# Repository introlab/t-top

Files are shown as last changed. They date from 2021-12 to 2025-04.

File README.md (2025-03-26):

# T-Top

T-Top is a tabletop robot designed with advanced audio and vision sensors, deep learning perceptual processing and
telecommunication capabilities to provide richer interaction modalities and develop higher cognitive abilities from
interacting with people.

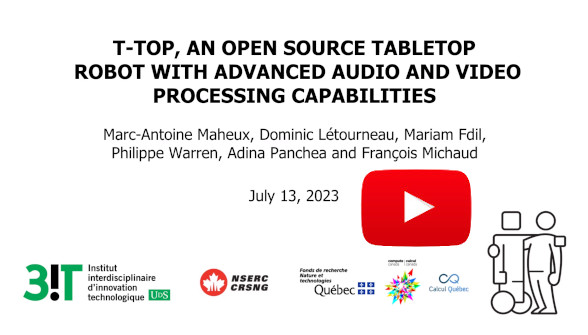
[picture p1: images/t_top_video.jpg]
T-Top (https://www.youtube.com/watch?v=2jpqTp6jozc)


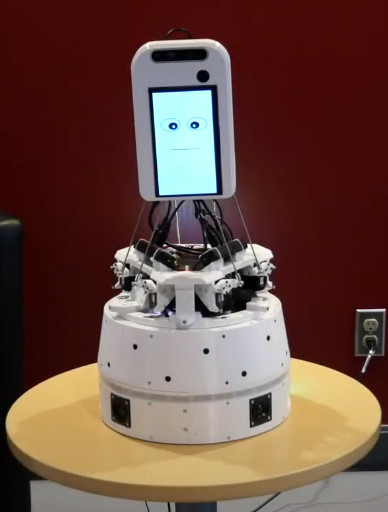
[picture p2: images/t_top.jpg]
T-Top


## Authors

- Marc-Antoine Maheux (@mamaheux)
- Dominic Létourneau (@doumdi)
- Philippe Warren (@philippewarren)
- Mariam Fdil (@MariamFdil)
- [François Michaud](mailto:francois.michaud@usherbrooke.ca), ing., Ph.D.

## Contributors

- Ian-Mathieu Joly (@joli-1801)
- Charles Caya (@chcaya)
- Alexandre Filion (@alexfilion)

## Licensing

- Source code files: [GPLv3](LICENSE_SOURCE_CODE)
- Other files: [Creative Commons Attribution-NonCommercial-ShareAlike 4.0 International Public License](LICENSE_OTHER)

## Features

| Category | Type | Description |
| --- | --- | --- |
| Power | Power Adapter | 19 V |
| | Battery | 1x [RRC2054-2](https://www.rrc-ps.com/en/battery-packs/standard-battery-packs/products/RRC2054-2) |
| | Battery Charger | 1x [RRC-PMM240](https://www.rrc-ps.com/en/battery-packs/standard-battery-packs/products/RRC-PMM240) |
| Sensors | Microphone Array  | 16x [xSoundsMicrophones](https://github.com/introlab/xSoundsMicrophones), 1x [16SoundsUSB](https://github.com/introlab/16SoundsUSB) |
| | RGB-D Camera | 1x [Intel RealSense D435i](https://www.intelrealsense.com/depth-camera-d435i/) |
| | Wide Angle Camera | 1x [Arducam AR0230](https://www.uctronics.com/arducam-1080p-hd-wide-angle-wdr-usb-camera-module-for-computer-2mp-1-2-7-cmos-ar0230-100-degree-mini-uvc-usb2-0-spy-webcam-board-with-3-3ft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) |
| | Touchscreen | 1x 7 inch 1024x600 capacitive touchscreen |
| | Current/Voltage | [INA220](https://www.ti.com/product/INA220) |
| | Light Sensors | 4x [Adafruit ALS-PT19 ](https://www.adafruit.com/product/2748) |
| | Buttons | 4x buttons |
| Actuators | Stewart Platform  | Displacement range: ±3 cm (x, y and z), ±20° (x and y), ±30° (z). Motor: [Dynamixel XL430-W250](https://emanual.robotis.com/docs/en/dxl/x/xl430-w250/) | |
| | Rotating Base | Displacement range: illimited. Motor: [Dynamixel XL430-W250](https://emanual.robotis.com/docs/en/dxl/x/xl430-w250/) |
| | Speakers | 4x [Dayton Audio DMA45-8](https://www.daytonaudio.com/product/1613/dma45-8-1-1-2-dual-magnet-aluminum-cone-full-range-driver-8-ohm), 2x [MAX9744](https://www.adafruit.com/product/1752) |
| | Cooling | 2x [Noctua NF-A4x20 5V](https://noctua.at/en/products/fan/nf-a4x20-5v) |
| | Touchscreen | 1x 7 inch 1024x600 capacitive touchscreen |
| | LED | Battery status, volume level, led strip |
| Network | WiFi | Intel Dual Band Wireless-AC 8265 NGW |
| | Ethernet | 100 Mbps |
| Processing | Computer | [NVIDIA Jetson AGX Xavier Developer Kit](https://developer.nvidia.com/embedded/jetson-agx-xavier-developer-kit) or [NVIDIA Jetson AGX Xavier Orin Developer Kit](https://developer.nvidia.com/embedded/jetson-agx-orin-developer-kit) |
| | Motor MCU | [Teensy 4.0](https://www.pjrc.com/store/teensy40.html) |
| | Battery MCU | [Teensy LC](https://www.pjrc.com/teensy/teensyLC.html) |
| Perceptions | | SLAM, object detection, person pose estimation, face recognition, sound classification, speaker identification, robot name detection, speech to text, person identification, music beat detection, source source localization, ego noise reduction, vad |
| Behaviors | | Telepresence, emotions, talking, greeting, face following, dancing, exploring, sound following |

## Repository Structure

- The [documentation](documentation) folder contains the documentation to build and configure T-Top.
- The [CAD](CAD) folder contains the SolidWorks files of the robot. Il also contains the DXF and STL files to cut and
  print custom parts.
- The [firmwares](firmwares) folder contains the firmware for the MCUs.
- The [PCB](PCB) folder contains the KiCad files of the custom PCBs. Il also contains the Gerber files to manufacture
  the PCBs.
- The [ros](ros) folder contains the ROS packages to use the robot.
- The [tools](tools) folder contains the tools to develop and use the robot.

## Development Computer Setup

See [01_COMPUTER_CONFIGURATION.md](documentation/assembly/01_COMPUTER_CONFIGURATION.md#development-computer-ubuntu-2004)

## Papers

- [M.-A. Maheux, D. Létourneau, P. Warren, A. M. Panchea, J. M. Robillard and F. Michaud, “‍Designing a Tabletop SAR as an Advanced HRI Experimentation Platform,” in Proceedings of the 2024 International Symposium on Technological Advances in Human-Robot Interaction (TAHRI 2024), Boulder, CO, USA, 2024](https://dl.acm.org/doi/10.1145/3648536.3648538)
    - [YouTube Video](https://youtu.be/HSd65F055VE)
- [M. Fdil, M. Levasseur, D. Létourneau, M.-A. Maheux, M. Lussier-Therrien, F. Michaud, "Enhancing Open Conversations Using Visual Percepts From a Socially Assistive Robot -- Preliminary Assessment", in Proceedings of the International Conference on Social Robotics, 2024, pp. 1-12.](https://link.springer.com/chapter/10.1007/978-981-96-3519-1_17)
    - [YouTube Video](https://youtu.be/4ykoxQKUweU)  
- [A. M. Panchea, M.-A. Maheux, P. Warren, D. Létourneau and F. Michaud, “Exploratory Evaluation of a Tabletop Robot With Older Adults,” in Proceedings of the 2024 ACM/IEEE International Conference on Human-Robot Interaction, Boulder, CO, USA, 2024, pp. 817–821.](https://dl.acm.org/doi/10.1145/3610978.3640621)
- [M.-A. Maheux, A. M. Panchea, P. Warren, D. Létourneau and F. Michaud, “T-Top, an Open Source Tabletop Robot with Advanced Onboard Audio, Vision and Deep Learning Capabilities,” in Proceedings of the 2023 IEEE/RSJ International Conference on Intelligent Robots and Systems (IROS), Detroit, MI, USA, 2023, pp. 7862-7869.](https://ieeexplore.ieee.org/abstract/document/10342252)
- [M.-A. Maheux, C. Caya, D. Létourneau and F. Michaud, “T-Top, a sar experimental platform,” in Proceedings of the 2022 ACM/IEEE International Conference on Human-Robot Interaction, 2022, pp. 904–908.](https://dl.acm.org/doi/abs/10.5555/3523760.3523902)

## Sponsor

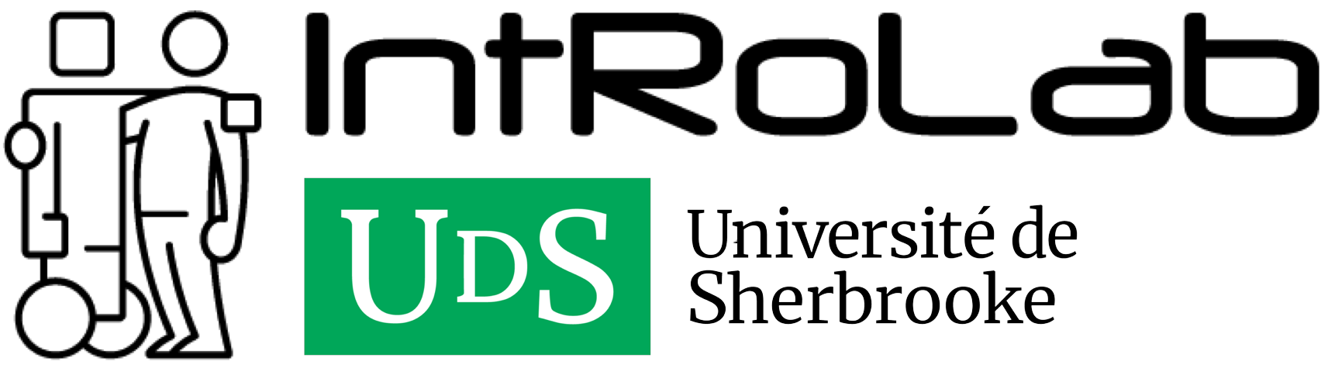
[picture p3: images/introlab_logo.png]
IntRoLab


[IntRoLab - Intelligent / Interactive / Integrated / Interdisciplinary Robot Lab](https://introlab.3it.usherbrooke.ca)

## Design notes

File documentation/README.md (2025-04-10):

# Documentation

## Folder Structure

- The [assembly](assembly/) folder contains the assembly instructions.
- The [protocols](protocols/) folder contains the communication protocols definitions.
- The [architecture](architecture/) folder contains architecture diagrams.
- The [tf](tf/) folder illustrates the frame locations.
- The [hbba_lite](hbba_lite/) folder contains the documentation of how to use HBBA Lite.
- The [getting_started](getting_started/) folder contains the documentation to get started with the robot.

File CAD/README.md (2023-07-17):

# CAD
This folder contains all mechanical-related files. The CAD have been done with SOLIDWORKS. If you don't have SOLIDWORKS, you can open the [STEP file](step/robot.STEP).

## Bill of Materials
 - [Parts](../documentation/assembly/00_ORDER_PRINT_LASER_CUTTING.md#bill-of-materials-excluding-custom-pcbs)
 - [3d Printing](../documentation/assembly/00_ORDER_PRINT_LASER_CUTTING.md#3d-printing)
 - [Laser Cutting](../documentation/assembly/00_ORDER_PRINT_LASER_CUTTING.md#laser-cutting)

## Folder Structure
SolidWorks files:
 - [3d printed parts](3d-printed-parts) contains the SolidWorks files for the 3D printed parts.
 - [assemblies](assemblies) contains the SolidWorks files for the assemblies. The robot assembly file is [robot.SLDASM](assemblies/robot.SLDASM).
 - [electronics](electronics) contains the SolidWorks files for all electronics parts.
 - [gazebo_meshes](gazebo%20meshes) contains the CAD files for the simulation.
 - [hardware](hardware) contains the SolidWorks files for screws, nuts, spacers and rods.
 - [laser](laser) contains the SolidWorks files for the laser cutted parts.
 - [step](step) contains the robot assembly in STEP format.

Manufacture files:
 - [DXF](DXF)
 - [STL](STL)

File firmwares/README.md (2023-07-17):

# Firmwares

T-Top uses two microcontrollers (MCU). This folder contains the firmwares for those.

## Folder Structure

- THe [common](common) folder contains common libraries.
- The [dynamixel_control](dynamixel_control) folder contains the firmware of the MCU that controls the motors.
- The [dynamixel_setup](dynamixel_setup)folder contains the firmware to setup the motors.
- The [psu_control](psu_control) folder contains the firmware of the MCU that controls and monitors the battery, audio
  amplifier, fans and LEDs.
- The [ego_noise_opencr_firmware](ego_noise_opencr_firmware) folder contains the firmware to get the ego noise data.

## Credits

The class `TrustRegionReflectiveSolver` in the [opencr_firmware](opencr_firmware) folder is heavily inspired
by [scipy.optimize.least_squares](https://docs.scipy.org/doc/scipy/reference/generated/scipy.optimize.least_squares.html)
.

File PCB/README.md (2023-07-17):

# PCB
To build T-Top, two cutom PCBs must be made.

## Folder Structure
- The [psu_control](psu_control) folder contains the PCB files for the PCB that controls and monitors the battery, audio amplifier, fans and LEDs.
- The [dynamixel_control](dynamixel_control) folder contains the PCB files for the PCB that controls the Dynamixel motors.
- The [buck_boost](buck_boost) folder contains the PCB files for the Buck-Boost PCB.
- The [t-top.pretty](t-top.pretty) folder contains the custom footprints.
- The [t-top.kicad_sym](t-top.kicad_sym) file contains the custom parts.

## PSU Control PCB
- [Schematic](psu_control/schematic.pdf)
- [Gerber](psu_control/gerber)
- [Bill of Materials](../documentation/assembly/00_ORDER_PRINT_LASER_CUTTING.md#psu-control-pcb)

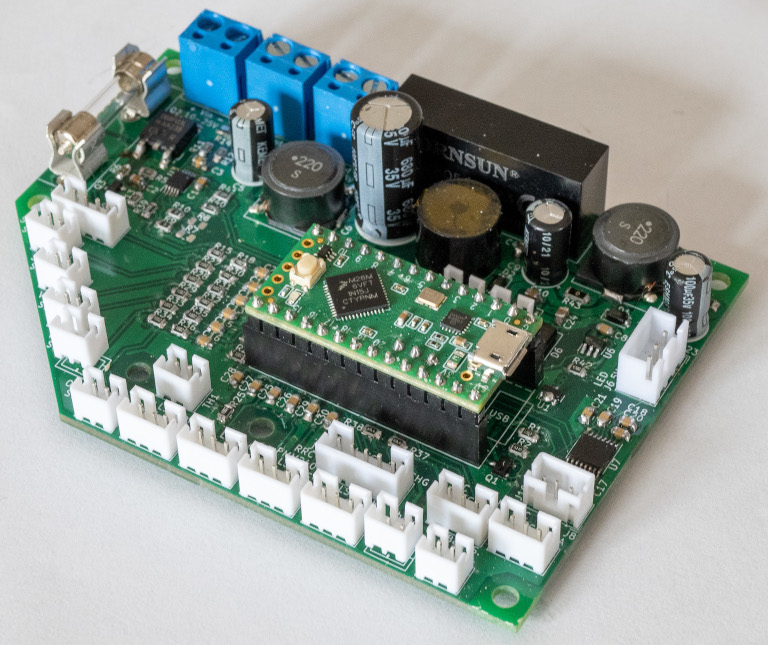
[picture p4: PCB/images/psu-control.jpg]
PSU Control PCB


## Dynamixel Control PCB
- [Schematic](dynamixel_control/schematic.pdf)
- [Gerber](dynamixel_control/gerber)
- [Bill of Materials](../documentation/assembly/00_ORDER_PRINT_LASER_CUTTING.md#dynamixel-control-pcb)

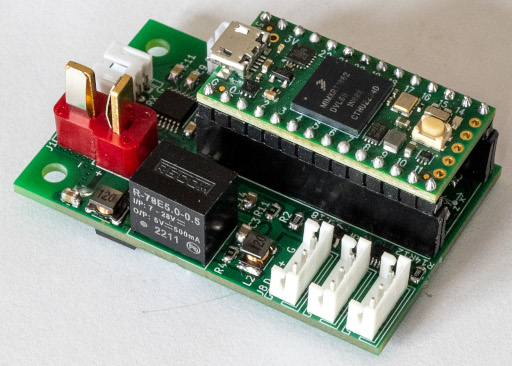
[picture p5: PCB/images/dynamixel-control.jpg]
Dynamixel Control PCB


## Buck-Boost PCB
- [Schematic](buck_boost/schematic.pdf)
- [Gerber](buck_boost/gerber)
- [Bill of Materials](../documentation/assembly/00_ORDER_PRINT_LASER_CUTTING.md#buck-boost-pcb)

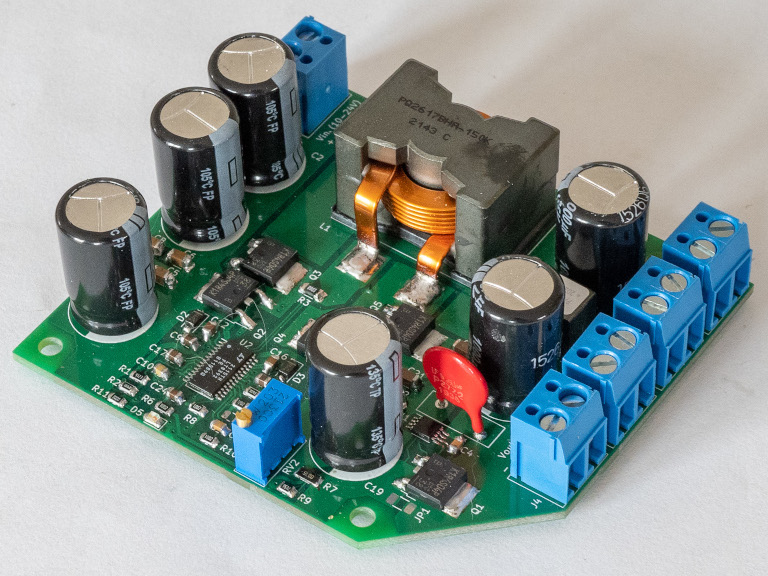
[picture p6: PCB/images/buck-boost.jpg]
Buck-Boost PCB


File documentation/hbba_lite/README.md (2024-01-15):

# HBBA Lite
HBBA (Hybrid Behavior-Based Architecture) is the control architecture of T-Top. A hybrid robot architecture means that perceptual nodes can communicate with the behavior nodes and the planning modules.
T-Top uses [HBBA Lite](https://github.com/introlab/hbba_lite/) implementation instead of the [original one](https://github.com/introlab/HBBA) since HBBA Lite is simpler to use but less complete.

## Core
See the [HBBA Lite documentation](https://github.com/introlab/hbba_lite#documentation).

## T-Top
The following sections present T-Top specific information.

### Resources
- `motor`: The resource to prevent conflicts over the motors.
- `audio`: The resource to prevent conflicts over the sound output.
- `led`: The resource to prevent conflicts over the LEDs.

### Desire Types
- [`Camera3dRecordingDesire`](../../ros/utils/t_top_hbba_lite/include/t_top_hbba_lite/Desires.h#L12): To enable the recording of the 3D camera.
- [`Camera2dWideRecordingDesire`](../../ros/utils/t_top_hbba_lite/include/t_top_hbba_lite/Desires.h#L22): To enable the recording of the 2D Wide camera.
- [`RobotNameDetectorDesire`](../../ros/utils/t_top_hbba_lite/include/t_top_hbba_lite/Desires.h#L32): To enable the robot name detector node.
- [`RobotNameDetectorWithLedStatusDesire`](../../ros/utils/t_top_hbba_lite/include/t_top_hbba_lite/Desires.h#L42): To enable the robot name detector node and have feed on the LED strip.
- [`SlowVideoAnalyzer3dDesire`](../../ros/utils/t_top_hbba_lite/include/t_top_hbba_lite/Desires.h#52): To enable the video analyzer node for the 3D camera at 1 Hz.
- [`FastVideoAnalyzer3dDesire`](../../ros/utils/t_top_hbba_lite/include/t_top_hbba_lite/Desires.h#L62): To enable the video analyzer node for the 3D camera at 5 Hz.
- [`FastVideoAnalyzer3dWithAnalyzedImageDesire`](../../ros/utils/t_top_hbba_lite/include/t_top_hbba_lite/Desires.h#L72): To enable the video analyzer node for the 3D camera at 5 Hz and to publish the analyzed image.
- [`SlowVideoAnalyzer2dWideDesire`](../../ros/utils/t_top_hbba_lite/include/t_top_hbba_lite/Desires.h#L82): To enable the video analyzer node for the 2D wide camera at 1 Hz.
- [`FastVideoAnalyzer2dWideDesire`](../../ros/utils/t_top_hbba_lite/include/t_top_hbba_lite/Desires.h#92): To enable the video analyzer node for the 2D wide camera at 5 Hz.
- [`FastVideoAnalyzer2dWideWithAnalyzedImageDesire`](../../ros/utils/t_top_hbba_lite/include/t_top_hbba_lite/Desires.h#L102): To enable the video analyzer node for the 2D wide camera at 5 Hz and to publish the analyzed image.
- [`AudioAnalyzerDesire`](../../ros/utils/t_top_hbba_lite/include/t_top_hbba_lite/Desires.h#L112): To enable the audio analyzer node.
- [`VadDesire`](../../ros/utils/t_top_hbba_lite/include/t_top_hbba_lite/Desires.h#L122): To enable to VAD node.
- [`SpeechToTextDesire`](../../ros/utils/t_top_hbba_lite/include/t_top_hbba_lite/Desires.h#L132): To enable the speech to text node.
- [`ExploreDesire`](../../ros/utils/t_top_hbba_lite/include/t_top_hbba_lite/Desires.h#L142): To enable the explore node.
- [`FaceAnimationDesire`](../../ros/utils/t_top_hbba_lite/include/t_top_hbba_lite/Desires.h#L152): To change the face animation.
- [`LedEmotionDesire`](../../ros/utils/t_top_hbba_lite/include/t_top_hbba_lite/Desires.h#L175): To enable the led emotion node.
- [`LedAnimationDesire`](../../ros/utils/t_top_hbba_lite/include/t_top_hbba_lite/Desires.h#L197): To enable the led animation node.
- [`SoundFollowingDesire`](../../ros/utils/t_top_hbba_lite/include/t_top_hbba_lite/Desires.h#L245): To enable the node that makes T-Top follow the loudest sound.
- [`NearestFaceFollowingDesire`](../../ros/utils/t_top_hbba_lite/include/t_top_hbba_lite/Desires.h#L255): To enable the node that makes T-Top follow the nearest face.
- [`SpecificFaceFollowingDesire`](../../ros/utils/t_top_hbba_lite/include/t_top_hbba_lite/Desires.h#L265): To enable the node that makes T-Top follow a specific face.
- [`SoundObjectPersonFollowingDesire`](../../ros/utils/t_top_hbba_lite/include/t_top_hbba_lite/Desires.h#L284): To enable the node that makes T-Top follow the loudest sound, the people and the objects.
- [`TalkDesire`](../../ros/utils/t_top_hbba_lite/include/t_top_hbba_lite/Desires.h#L294): To make T-Top talk.
- [`GestureDesire`](../../ros/utils/t_top_hbba_lite/include/t_top_hbba_lite/Desires.h#L313): To make T-Top perform a head gesture.
- [`DanceDesire`](../../ros/utils/t_top_hbba_lite/include/t_top_hbba_lite/Desires.h#L335): To make T-Top dance.
- [`PlaySoundDesire`](../../ros/utils/t_top_hbba_lite/include/t_top_hbba_lite/Desires.h#L345): To make T-Top play a sound file.
- [`TelepresenceDesire`](../../ros/utils/t_top_hbba_lite/include/t_top_hbba_lite/Desires.h#L364): To make T-Top perform a video call
- [`TeleoperationDesire`](../../ros/utils/t_top_hbba_lite/include/t_top_hbba_lite/Desires.h#L374): To enable remote control of T-Top.
- [`TooCloseReactionDesire`](../../ros/utils/t_top_hbba_lite/include/t_top_hbba_lite/Desires.h#L384): To enable the too near reaction behavior.

### Strategies
The strategies are declared in the following files: [Strategies.h](../../ros/utils/t_top_hbba_lite/include/t_top_hbba_lite/Strategies.h) and [Strategies.cpp](../../ros/utils/t_top_hbba_lite/src/Strategies.cpp).

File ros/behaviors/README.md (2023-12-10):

# Behavior Nodes

This folder contains ROS packages for the behavior nodes.

## Folder Structure

- The [dance](dance) folder contains the node to make T-Top dance.
- The [explore](explore) folder contains the node to make T-Top explore its surrounding.
- The [face_following](face_following) folder contains the node to make T-Top follow the nearest face.
- The [gesture](gesture) folder contains the node to make T-Top perform gestures.
- The [led_emotions](led_emotions) folder contains the node to make T-Top express emotion with its LED strip.
- The [led_animations](led_animations) folder contains the node to perform animations with the LED strip.
- The [sound_following](sound_following) folder contains the node to make T-Top follow the loudest sound.
- The [sound_object_person_following](sound_object_person_following) folder contains the node to make T-Top follow the loudest sound, the biggest (nearest) person and some objects.
- The [sound_player](sound_player) folder contains the node to play sound files.
- The [talk](talk) folder contains the node to make T-Top talk.
- The [piper_ros](piper_ros) folder contains the node to generate speech files with [Piper](https://github.com/rhasspy/piper).
- The [too_close_reaction](too_close_reaction) folder contains the node to move back the head when someone is too close to T-Top.

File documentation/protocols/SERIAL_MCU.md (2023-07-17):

# Serial MCU Communucation Protocol
This document presents the serial communication protocol between the MCUs and the computer.

## General Format
It is a binary protocol and all fields use little-endian ordering.

<table>
    <thead>
        <tr>
            <th colspan="9">Bytes</th>
        </tr>
    </thead>
    <thead>
        <tr>
            <th>1</th>
            <th>2</th>
            <th>3</th>
            <th>4</th>
            <th>5</th>
            <th>6</th>
            <th>7</th>
            <th>8</th>
        </tr>
    </thead>
    <tbody>
        <tr>
            <td colspan="4">Preamble</td>
            <td>Full Message Length</td>
            <td>Message Source Id</td>
            <td>Message Destination Id</td>
            <td>Acknowledgment Needed</td>
        </tr>
        <tr>
            <td colspan="2">Message Id</td>
            <td colspan="2">Message Type</td>
            <td colspan="4">Payload</td>
        </tr>
        <tr>
            <td colspan="8">...</td>
        </tr>
        <tr>
            <td>CRC8</td>
            <td colspan="7"></td>
        </tr>
    </tbody>
</table>

### Field Description
| Field Name | Type | Description |
| --- | --- | --- |
| Preamble | uint32 | This field is used to detect the beginning of a message (0xAAAAAAAA). |
| Full Message Length | uint8  | This field is equal to the message length in bytes including this field and without the preamble. |
| Message Source Id | uint8  | This field contains the device id of the source device. |
| Message Destination Id | uint8  | This field contains the device id of the destination device. |
| Acknowledgment Needed  | bool | This field indicates if an acknowledgment is needed). |
| Message Id | uint16 | This field contains a random id identifying the message. |
| Message Type | uint16 | This field contains the message type. |
| Payload | | The payload depends on the message type. |
| CRC8 | uint8  | This field contains the CRC8 value excluding this field. |

### Device Id Descriptions
| Device Id | Name |
| --- | --- |
| 0 | PSU Control |
| 1 | Dynamixel Control |
| 2 | Computer |

### Message Types
| Message Type | Name | Source | Destination | Description |
| --- | --- | --- | --- | --- |
| 0 | [Acknowledgment](#acknowledgment-payload) | Any | Any | This message indicates that a message is received. |
| 1 | [Base Status](#base-Status-payload) | PSU Control | Computer | This message contains the status of the base. |
| 2 | [Button Pressed](#button-pressed-payload) | PSU Control | Computer | This message indicates that a button is pressed. |
| 3 | [Set Volume](#set-volume-payload) | Computer | PSU Control | This message sets the volume of the audio amplifier. |
| 4 | [Set LED Colors](#set-led-colors-payload) | Computer | PSU Control | This message sets the LED colors of the base. |
| 5 | [Motor Status](#motor-status-payload) | Dynamixel Control | Computer | This message contains the status of all motors. |
| 6 | [IMU Data](#imu-data-payload) | Dynamixel Control | Computer | This message contains the IMU data. |
| 7 | [Set Torso Orientation](#set-torso-orientation-payload) | Computer | Dynamixel Control | This message sets the torso orientation. |
| 8 | [Set Head Pose](#set-head-pose-payload) | Computer | Dynamixel Control | This message sets the head pose. |
| 9 | Shutdown | PSU Control | Computer/Dynamixel Control | This message indicates that the computer must shut down. This message has no payload. |

### Behaviors
- All receivers check the preamble to detect the beginning of a message. So, a byte can be missed and the receivers are not out of synchronization with the senders. Only the message containing the missing byte is dropped.
- All devices route the message according to the destination id.
- The message is dropped if the destination id is invalid.
- The message is dropped if the source id is invalid.
- The message is dropped if the CRC8 is invalid.
- The message is dropped if the length does not match the message type.
- The destination device sends an acknowledgment to the source device if the CRC8 is valid.

## Acknowledgment Payload
This message indicates that a message is received.

<table>
    <thead>
        <tr>
            <th colspan="2">Bytes</th>
        </tr>
    </thead>
    <thead>
        <tr>
            <th>1</th>
            <th>2</th>
        </tr>
    </thead>
    <tbody>
        <tr>
            <td colspan="2">Received Message Id</td>
        </tr>
    </tbody>
</table>

### Field Description
| Field Name | Type | Description |
| --- | --- | --- |
| Received Message Id | uint16 | This field contains the received message id. |

## Base Status Payload
This message contains the status of the base.

<table>
    <thead>
        <tr>
            <th colspan="8">Bytes</th>
        </tr>
    </thead>
    <thead>
        <tr>
            <th>1</th>
            <th>2</th>
            <th>3</th>
            <th>4</th>
            <th>5</th>
            <th>6</th>
            <th>7</th>
            <th>8</th>
        </tr>
    </thead>
    <tbody>
        <tr>
            <td>Is PSU Connected</td>
            <td>Has Charger Error</td>
            <td>Is Battery Charging</td>
            <td>Has Battery Error</td>
            <td colspan="4">State of Charge</td>
        </tr>
        <tr>
            <td colspan="4">Current</td>
            <td colspan="4">Voltage</td>
        </tr>
        <tr>
            <td colspan="4">Onboard Temperature</td>
            <td colspan="4">External Temperature</td>
        </tr>
        <tr>
            <td colspan="4">Front Light Sensor</td>
            <td colspan="4">Back Light Sensor</td>
        </tr>
        <tr>
            <td colspan="4">Left Light Sensor</td>
            <td colspan="4">Right Light Sensor</td>
        </tr>
        <tr>
            <td>Volume</td>
            <td>Maximum Volume</td>
            <td colspan="6"></td>
        </tr>
    </tbody>
</table>

### Field Description
| Field Name | Type | Description |
| --- | --- | --- |
| Is PSU Connected | bool | This field indicates whether the PSU is connected to the robot. |
| Has Charger Error | bool | This field indicates whether there is a charger error. |
| Is Battery Charging | bool | This field indicates whether the battery is charging. |
| Has Battery Error | bool | This field indicates whether there is a battery error. |
| State of Charge | float  | This field contains the actual battery state of charge in percent (0 to 100). |
| Current | float  | This field contains the actual current in A. |
| Voltage | float  | This field contains the actual voltage in V. |
| Onboard Temperature | float  | This field contains the actual temperature in °C on the PSU Control PCB. |
| External Temperature | float  | This field contains the actual temperature in °C in the base (invalid). |
| Front Light Sensor | float  | This field contains the front light level (0 to 1). |
| Back Light Sensor | float  | This field contains the back light level (0 to 1). |
| Left Light Sensor | float  | This field contains the left light level (0 to 1). |
| Right Light Sensor | float  | This field contains the right light level (0 to 1). |
| Volume | uint8  | This field contains the actual volume (0 to 63). |
| Maximum Volume | uint8  | This field contains the actual volume maximum (0 to 63). The maximum depends on whether the power supply is connected. |

## Button Pressed Payload
This message indicates that a button is pressed.

<table>
    <thead>
        <tr>
            <th>Bytes</th>
        </tr>
    </thead>
    <thead>
        <tr>
            <th>1</th>
        </tr>
    </thead>
    <tbody>
        <tr>
            <td>Button Id</td>
        </tr>
    </tbody>
</table>

### Field Description
| Field Name | Type  | Description |
| --- | ----- | --- |
| Button Id  | uint8 | This field indicates which button was pressed (start or stop). |

### Device Id Descriptions
| Button Id | Name  |
| --- | ----- |
| 0 | Start |
| 1 | End |

## Set Volume Payload
This message sets the volume of the audio amplifier.

<table>
    <thead>
        <tr>
            <th>Bytes</th>
        </tr>
    </thead>
    <thead>
        <tr>
            <th>1</th>
        </tr>
    </thead>
    <tbody>
        <tr>
            <td>Volume</td>
        </tr>
    </tbody>
</table>

### Field Description
| Field Name | Type  | Description |
| --- | ----- | --- |
| Volume | uint8 | This field contains the new volume (0 to 63). |

## Set LED Colors Payload
This message sets the volume of the audio amplifier.

<table>
    <thead>
        <tr>
            <th colspan="8">Bytes</th>
        </tr>
    </thead>
    <thead>
        <tr>
            <th>1</th>
            <th>2</th>
            <th>3</th>
            <th>4</th>
            <th>5</th>
            <th>6</th>
            <th>7</th>
            <th>8</th>
        </tr>
    </thead>
    <tbody>
        <tr>
            <td>LED 1 Red Value</td>
            <td>LED 1 Green Value</td>
            <td>LED 1 Blue Value</td>
            <td>LED 2 Red Value</td>
            <td>LED 2 Green Value</td>
            <td>LED 2 Blue Value</td>
            <td colspan="2">...</td>
        </tr>
    </tbody>
</table>

### Field Description
| Field Name | Type  | Description |
| --- | ----- | --- |
| LED 1 Red Value | uint8 | This field contains the LED 1 red value (0 to 255). |
| LED 1 Green Value | uint8 | This field contains the LED 1 red value (0 to 255). |
| LED 1 Blue Value  | uint8 | This field contains the LED 1 red value (0 to 255). |
| LED 2 Red Value | uint8 | This field contains the LED 2 red value (0 to 255). |
| LED 2 Green Value | uint8 | This field contains the LED 2 red value (0 to 255). |
| LED 2 Blue Value  | uint8 | This field contains the LED 2 red value (0 to 255). |
| ... | | Those fields are repeated for each led. There are 31 LEDs |

## Motor Status Payload
This message contains the status of all motors.

<table>
    <thead>
        <tr>
            <th colspan="8">Bytes</th>
        </tr>
    </thead>
    <thead>
        <tr>
            <th>1</th>
            <th>2</th>
            <th>3</th>
            <th>4</th>
            <th>5</th>
            <th>6</th>
            <th>7</th>
            <th>8</th>
        </tr>
    </thead>
    <tbody>
        <tr>
            <td colspan="4">Torso Orientation</td>
            <td colspan="2">Torso Servo Speed</td>
            <td colspan="2">Head Servo Angle 1</td>
        </tr>
        <tr>
            <td colspan="2">Head Servo Angle 1</td>
            <td colspan="4">Head Servo Angle 2</td>
            <td colspan="2">Head Servo Angle 3</td>
        </tr>
        <tr>
            <td colspan="2">Head Servo Angle 3</td>
            <td colspan="4">Head Servo Angle 4</td>
            <td colspan="2">Head Servo Angle 5</td>
        </tr>
        <tr>
            <td colspan="2">Head Servo Angle 5</td>
            <td colspan="4">Head Servo Angle 6</td>
            <td colspan="2">Head Servo Speed 1</td>
        </tr>
        <tr>
            <td colspan="2">Head Servo Speed 2</td>
            <td colspan="2">Head Servo Speed 3</td>
            <td colspan="2">Head Servo Speed 4</td>
            <td colspan="2">Head Servo Speed 5</td>
        </tr>
        <tr>
            <td colspan="2">Head Servo Speed 6</td>
            <td colspan="4">Head Pose Position X</td>
            <td colspan="2">Head Pose Position Y</td>
        </tr>
        <tr>
            <td colspan="2">Head Pose Position Y</td>
            <td colspan="4">Head Pose Position Z</td>
            <td colspan="2">Head Pose Orientation W</td>
        </tr>
        <tr>
            <td colspan="2">Head Pose Orientation W</td>
            <td colspan="4">Head Pose Orientation X</td>
            <td colspan="2">Head Pose Orientation Y</td>
        </tr>
        <tr>
            <td colspan="2">Head Pose Orientation Y</td>
            <td colspan="4">Head Pose Orientation Z</td>
            <td>Is Head Pose Reachable</td>
            <td></td>
        </tr>
    </tbody>
</table>

### Field Description
| Field Name | Type  | Description |
| --- | ----- | --- |
| Torso Orientation | float | This field contains the actual torso orientation in radian (0 to 2PI). |
| Torso Servo Speed | int16 | This field contains the actual torso servo speed in 0.229 rpm (-1023 to 1023). |
| Head Servo Angle 1 | float | This field contains the actual head servo angle 1 in radian (0 to 2PI). |
| Head Servo Angle 2 | float | This field contains the actual head servo angle 2 in radian (0 to 2PI). |
| Head Servo Angle 3 | float | This field contains the actual head servo angle 3 in radian (0 to 2PI). |
| Head Servo Angle 4 | float | This field contains the actual head servo angle 4 in radian (0 to 2PI). |
| Head Servo Angle 5 | float | This field contains the actual head servo angle 5 in radian (0 to 2PI). |
| Head Servo Angle 6 | float | This field contains the actual head servo angle 6 in radian (0 to 2PI). |
| Head Servo Speed 1 | int16 | This field contains the actual head servo speed 1 in 0.229 rpm (-1023 to 1023). |
| Head Servo Speed 2 | int16 | This field contains the actual head servo speed 2 in 0.229 rpm (-1023 to 1023). |
| Head Servo Speed 3 | int16 | This field contains the actual head servo speed 3 in 0.229 rpm (-1023 to 1023). |
| Head Servo Speed 4 | int16 | This field contains the actual head servo speed 4 in 0.229 rpm (-1023 to 1023). |
| Head Servo Speed 5 | int16 | This field contains the actual head servo speed 5 in 0.229 rpm (-1023 to 1023). |
| Head Servo Speed 6 | int16 | This field contains the actual head servo speed 6 in 0.229 rpm (-1023 to 1023). |
| Head Pose Position X | float | This field contains the actual X head position in meters in frame `stewart_base`. |
| Head Pose Position Y | float | This field contains the actual Y head position in meters in frame `stewart_base`. |
| Head Pose Position Z | float | This field contains the actual Z head position in meters in frame `stewart_base`. |
| Head Pose Orientation W | float | This field contains the actual W head orientation in meters in frame `stewart_base`. |
| Head Pose Orientation X | float | This field contains the actual X head orientation in meters in frame `stewart_base`. |
| Head Pose Orientation Y | float | This field contains the actual Y head orientation in meters in frame `stewart_base`. |
| Head Pose Orientation Z | float | This field contains the actual Z head orientation in meters in frame `stewart_base`. |
| Is Head Pose Reachable  | bool  | This field indicates if the last desired head pose is reachable. |

## IMU Data Payload
This message contains the status of all motors.

<table>
    <thead>
        <tr>
            <th colspan="8">Bytes</th>
        </tr>
    </thead>
    <thead>
        <tr>
            <th>1</th>
            <th>2</th>
            <th>3</th>
            <th>4</th>
            <th>5</th>
            <th>6</th>
            <th>7</th>
            <th>8</th>
        </tr>
    </thead>
    <tbody>
        <tr>
            <td colspan="4">Acceleration X</td>
            <td colspan="4">Acceleration Y</td>
        </tr>
        <tr>
            <td colspan="4">Acceleration Z</td>
            <td colspan="4">Angular Rate X</td>
        </tr>
        <tr>
            <td colspan="4">Angular Rate Y</td>
            <td colspan="4">Angular Rate Z</td>
        </tr>
    </tbody>
</table>

### Field Description
| Field Name | Type  | Description |
| --- | ----- | --- |
| Acceleration X | float | This field contains the actual IMU X Acceleration in m/s².  |
| Acceleration Y | float | This field contains the actual IMU Y Acceleration in m/s².  |
| Acceleration Z | float | This field contains the actual IMU Z Acceleration in m/s².  |
| Angular Rate X | float | This field contains the actual IMU X Angular Rate in rad/s. |
| Angular Rate Y | float | This field contains the actual IMU X Angular Rate in rad/s. |
| Angular Rate Z | float | This field contains the actual IMU X Angular Rate in rad/s. |

## Set Torso Orientation Payload
This message sets the torso orientation.

<table>
    <thead>
        <tr>
            <th colspan="8">Bytes</th>
        </tr>
    </thead>
    <thead>
        <tr>
            <th>1</th>
            <th>2</th>
            <th>3</th>
            <th>4</th>
        </tr>
    </thead>
    <tbody>
        <tr>
            <td colspan="4">Torso Orientation</td>
        </tr>
    </tbody>
</table>

### Field Description
| Field Name | Type  | Description |
| --- | ----- | --- |
| Torso Orientation | float | This field contains the new torso orientation in radian (0 to 2PI). |

## Set Head Pose Payload
This message sets the head pose.

<table>
    <thead>
        <tr>
            <th colspan="8">Bytes</th>
        </tr>
    </thead>
    <thead>
        <tr>
            <th>1</th>
            <th>2</th>
            <th>3</th>
            <th>4</th>
            <th>5</th>
            <th>6</th>
            <th>7</th>
            <th>8</th>
        </tr>
    </thead>
    <tbody>
        <tr>
            <td colspan="4">Head Pose Position X</td>
            <td colspan="4">Head Pose Position Y</td>
        </tr>
        <tr>
            <td colspan="4">Head Pose Position Z</td>
            <td colspan="4">Head Pose Orientation W</td>
        </tr>
        <tr>
            <td colspan="4">Head Pose Orientation X</td>
            <td colspan="4">Head Pose Orientation Y</td>
        </tr>
        <tr>
            <td colspan="4">Head Pose Orientation Z</td>
            <td colspan="4"></td>
        </tr>
    </tbody>
</table>

### Field Description
| Field Name | Type  | Description |
| --- | ----- | --- |
| Head Pose Position X | float | This field contains the new X head position in meters in frame `stewart_base`. |
| Head Pose Position Y | float | This field contains the new Y head position in meters in frame `stewart_base`. |
| Head Pose Position Z | float | This field contains the new Z head position in meters in frame `stewart_base`. |
| Head Pose Orientation W | float | This field contains the new W head orientation in meters in frame `stewart_base`. |
| Head Pose Orientation X | float | This field contains the new X head orientation in meters in frame `stewart_base`. |
| Head Pose Orientation Y | float | This field contains the new Y head orientation in meters in frame `stewart_base`. |
| Head Pose Orientation Z | float | This field contains the new Z head orientation in meters in frame `stewart_base`. |

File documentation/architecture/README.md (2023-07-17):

# Architecture
This folder contains architecture diagrams. All diagrams have been done with [diagrams.net](diagrams.net).

## Electrical Block Diagram
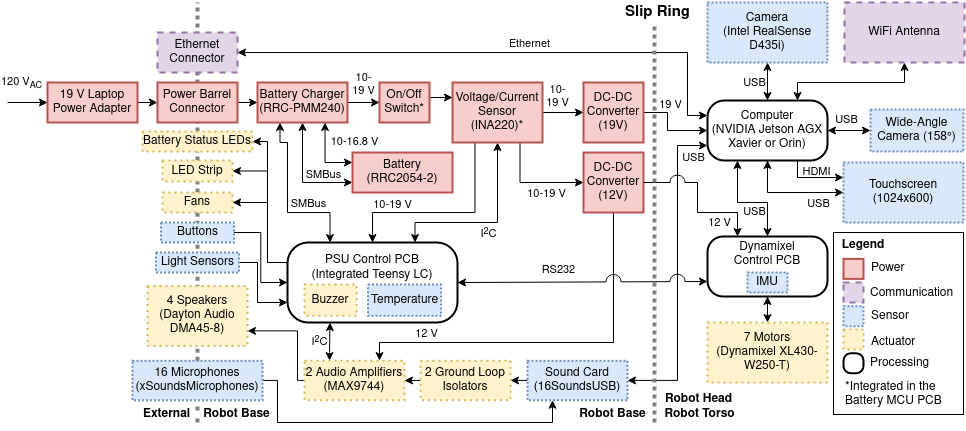
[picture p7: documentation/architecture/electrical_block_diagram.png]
Electrical Block Diagram


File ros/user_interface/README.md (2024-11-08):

# user_interface

This folder contains the web user interface for the robot face.

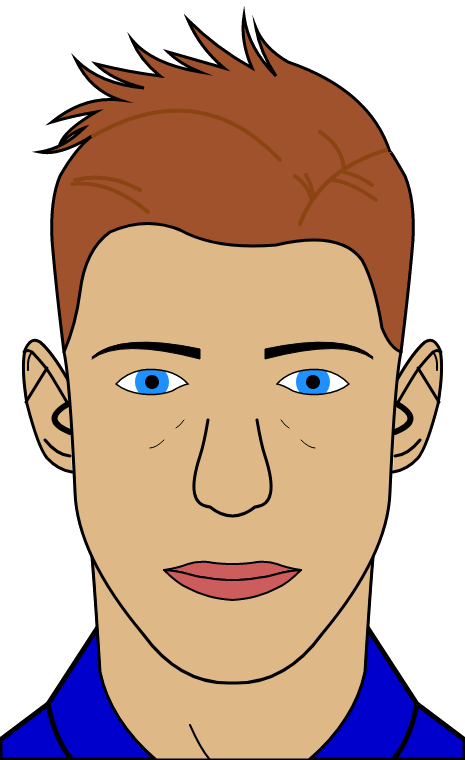
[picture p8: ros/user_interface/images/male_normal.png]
Male

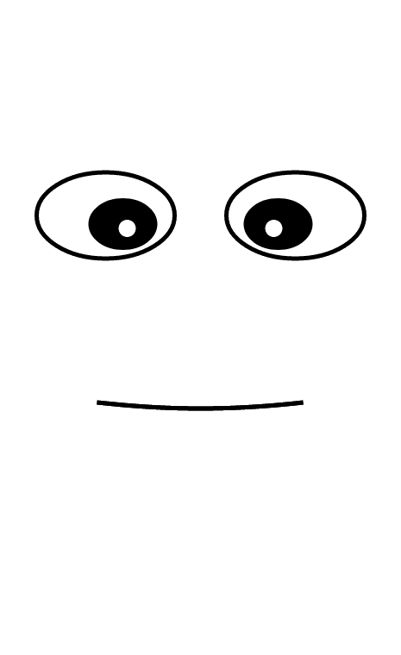
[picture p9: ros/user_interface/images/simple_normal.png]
Simple


## Package setup

```
npm install
```

## Compiles and hot-reloads for development

```
npm run serve
```

## Published Topics

- `face/animation` ([std_msgs/String](https://docs.ros.org/en/humble/p/std_msgs/interfaces/msg/String.html)): Indicates the
  actual animation.
- `face/mouth_signal_scale` ([std_msgs/Float32](https://docs.ros.org/en/humble/p/std_msgs/interfaces/msg/Float32.html)):
  Indicates how much the mouth must be open.

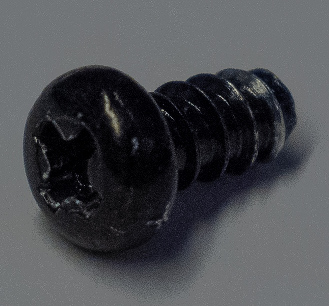
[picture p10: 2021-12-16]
documentation/assembly/images/hardware/dynamixel-screw.jpg

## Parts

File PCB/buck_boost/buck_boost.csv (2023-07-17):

Source: | /home/marc-antoine/Bureau/Maitrîse/t-top_ws/src/t-top/PCB/buck_boost/buck_boost.kicad_sch
Date: | lun 17 avr 2023 14:18:07
Tool: | Eeschema 6.0.11-2627ca5db0~126~ubuntu20.04.1
Generator: | /usr/share/kicad/plugins/bom_csv_grouped_by_value.py
Component Count: | 57
Individual Components:
Item | Qty | Reference(s) | Value | LibPart | Footprint | Datasheet
 |  | C1 | 1000µF/35V | Device:CP | Capacitor_THT:CP_Radial_D12.5mm_P5.00mm
 |  | C2 | 1000µF/35V | Device:CP | Capacitor_THT:CP_Radial_D12.5mm_P5.00mm
 |  | C3 | 1000µF/35V | Device:CP | Capacitor_THT:CP_Radial_D12.5mm_P5.00mm
 |  | C4 | 47nF/35V | Device:C | Capacitor_SMD:C_0805_2012Metric | ~
 |  | C5 | 10µF/35V | Device:C | Capacitor_SMD:C_1206_3216Metric | ~
 |  | C6 | 10µF/35V | Device:C | Capacitor_SMD:C_1206_3216Metric | ~
 |  | C7 | 10µF/35V | Device:C | Capacitor_SMD:C_1206_3216Metric | ~
 |  | C8 | 10µF/35V | Device:C | Capacitor_SMD:C_1206_3216Metric | ~
 |  | C9 | 1µF/35V | Device:C | Capacitor_SMD:C_0805_2012Metric | ~
 |  | C10 | 0.47µF/16V | Device:C | Capacitor_SMD:C_0805_2012Metric | ~
 |  | C11 | 1000µF/35V | Device:CP | Capacitor_THT:CP_Radial_D12.5mm_P5.00mm
 |  | C12 | 2.2µF/16V | Device:C | Capacitor_SMD:C_0805_2012Metric | ~
 |  | C13 | 220nF/16V | Device:C | Capacitor_SMD:C_0805_2012Metric | ~
 |  | C14 | 27nF/16V | Device:C | Capacitor_SMD:C_0805_2012Metric | ~
 |  | C15 | NI | Device:C | Capacitor_SMD:C_0805_2012Metric | ~
 |  | C16 | 2.2µF/16V | Device:C | Capacitor_SMD:C_0805_2012Metric | ~
 |  | C17 | 4.7µF/16V | Device:C | Capacitor_SMD:C_0805_2012Metric | ~
 |  | C18 | 1µF/35V | Device:C | Capacitor_SMD:C_0805_2012Metric | ~
 |  | C19 | 470µF/35V | Device:CP | Capacitor_THT:CP_Radial_D12.5mm_P5.00mm
 |  | C20 | 22µF/35V | Device:C | Capacitor_SMD:C_1206_3216Metric | ~
 |  | C21 | 22µF/35V | Device:C | Capacitor_SMD:C_1206_3216Metric | ~
 |  | C22 | 22µF/35V | Device:C | Capacitor_SMD:C_1206_3216Metric | ~
 |  | C23 | 22µF/35V | Device:C | Capacitor_SMD:C_1206_3216Metric | ~
 |  | C24 | 1µF/35V | Device:C | Capacitor_SMD:C_0805_2012Metric | ~
 |  | C25 | 1000µF/35V | Device:CP | Capacitor_THT:CP_Radial_D12.5mm_P5.00mm
 |  | D2 | SS2040LL | Device:D_Schottky | Diode_SMD:D_SOD-123F | ~
 |  | D3 | SS2040LL | Device:D_Schottky | Diode_SMD:D_SOD-123F | ~
 |  | D5 | LED | Device:LED | Diode_SMD:D_0805_2012Metric | ~
 |  | J1 | VIN 10-24V | Connector:Conn_01x02_Male | t-top:OSTTA020161 | ~
 |  | J2 | VOUT | Connector:Conn_01x02_Male | t-top:OSTTA020161 | ~
 |  | J3 | VOUT | Connector:Conn_01x02_Male | t-top:OSTTA020161 | ~
 |  | J4 | VOUT | Connector:Conn_01x02_Male | t-top:OSTTA020161 | ~
 |  | J5 | VOUT | Connector:Conn_01x02_Male | t-top:OSTTA020161 | ~
 |  | JP1 | Jumper | Device:Jumper | Resistor_SMD:R_1206_3216Metric
 |  | L1 | 15µH (PQ2617BHA-150K) | Device:L | t-top:PQ2617BHA-150K | ~
 |  | L2 | 1µH (PA4987.102HLT) | Device:L | t-top:PA4987.XXXHL | ~
 |  | Q1 | TK1R4S04PB | Device:Q_NMOS_GDS | Package_TO_SOT_SMD:TO-252-2 | ~
 |  | Q2 | TK1R4S04PB | Device:Q_NMOS_GDS | Package_TO_SOT_SMD:TO-252-2 | ~
 |  | Q3 | TK1R4S04PB | Device:Q_NMOS_GDS | Package_TO_SOT_SMD:TO-252-2 | ~
 |  | Q4 | TK1R4S04PB | Device:Q_NMOS_GDS | Package_TO_SOT_SMD:TO-252-2 | ~
 |  | Q5 | TK1R4S04PB | Device:Q_NMOS_GDS | Package_TO_SOT_SMD:TO-252-2 | ~
 |  | R1 | 412k | Device:R | Resistor_SMD:R_0805_2012Metric | ~
 |  | R2 | 80.6k | Device:R | Resistor_SMD:R_0805_2012Metric | ~
 |  | R3 | 0.003/1W | Device:R | Resistor_SMD:R_1206_3216Metric | ~
 |  | R4 | 12k | Device:R | Resistor_SMD:R_0805_2012Metric | ~
 |  | R5 | 309k | Device:R | Resistor_SMD:R_0805_2012Metric | ~
 |  | R6 | 10k | Device:R | Resistor_SMD:R_0805_2012Metric | ~
 |  | R7 | RIS | Device:R | Resistor_SMD:R_1206_3216Metric | ~
 |  | R8 | 10k | Device:R | Resistor_SMD:R_0805_2012Metric | ~
 |  | R9 | FB3 | Device:R | Resistor_SMD:R_0805_2012Metric | ~
 |  | R10 | 10k | Device:R | Resistor_SMD:R_0805_2012Metric | ~
 |  | R11 | 301 | Device:R | Resistor_SMD:R_0805_2012Metric | ~
 |  | R12 | 0 | Device:R | Resistor_SMD:R_1206_3216Metric | ~
 |  | RV1 | V27ZA2P | Device:Varistor | Varistor:RV_Disc_D12mm_W4.2mm_P7.5mm | ~
 |  | RV2 | 20k | Device:R_POT | Potentiometer_THT:Potentiometer_Bourns_3296W_Vertical
 |  | U1 | LTC4359-MS8 | Power_Management:LTC4359-MS8 | Package_SO:MSOP-8_3x3mm_P0.65mm | https://www.analog.com/media/en/technical-documentation/data-sheets/ltc4359.pdf
 |  | U2 | LT8392 | t-top:LT8392 | Package_SO:TSSOP-28-1EP_4.4x9.7mm_P0.65mm
Collated Components:
Item | Qty | Reference(s) | Value | LibPart | Footprint | Datasheet
1 | 5 | C1, C2, C3, C11, C25 | 1000µF/35V | Device:CP | Capacitor_THT:CP_Radial_D12.5mm_P5.00mm
2 | 1 | C4 | 47nF/35V | Device:C | Capacitor_SMD:C_0805_2012Metric | ~
3 | 4 | C5, C6, C7, C8 | 10µF/35V | Device:C | Capacitor_SMD:C_1206_3216Metric | ~
4 | 3 | C9, C18, C24 | 1µF/35V | Device:C | Capacitor_SMD:C_0805_2012Metric | ~
5 | 1 | C10 | 0.47µF/16V | Device:C | Capacitor_SMD:C_0805_2012Metric | ~
6 | 2 | C12, C16 | 2.2µF/16V | Device:C | Capacitor_SMD:C_0805_2012Metric | ~
7 | 1 | C13 | 220nF/16V | Device:C | Capacitor_SMD:C_0805_2012Metric | ~
8 | 1 | C14 | 27nF/16V | Device:C | Capacitor_SMD:C_0805_2012Metric | ~
9 | 1 | C15 | NI | Device:C | Capacitor_SMD:C_0805_2012Metric | ~
10 | 1 | C17 | 4.7µF/16V | Device:C | Capacitor_SMD:C_0805_2012Metric | ~
11 | 1 | C19 | 470µF/35V | Device:CP | Capacitor_THT:CP_Radial_D12.5mm_P5.00mm
12 | 4 | C20, C21, C22, C23 | 22µF/35V | Device:C | Capacitor_SMD:C_1206_3216Metric | ~
13 | 2 | D2, D3 | SS2040LL | Device:D_Schottky | Diode_SMD:D_SOD-123F | ~
14 | 1 | D5 | LED | Device:LED | Diode_SMD:D_0805_2012Metric | ~
15 | 1 | J1 | VIN 10-24V | Connector:Conn_01x02_Male | t-top:OSTTA020161 | ~
16 | 4 | J2, J3, J4, J5 | VOUT | Connector:Conn_01x02_Male | t-top:OSTTA020161 | ~
17 | 1 | JP1 | Jumper | Device:Jumper | Resistor_SMD:R_1206_3216Metric
18 | 1 | L1 | 15µH (PQ2617BHA-150K) | Device:L | t-top:PQ2617BHA-150K | ~
19 | 1 | L2 | 1µH (PA4987.102HLT) | Device:L | t-top:PA4987.XXXHL | ~
20 | 5 | Q1, Q2, Q3, Q4, Q5 | TK1R4S04PB | Device:Q_NMOS_GDS | Package_TO_SOT_SMD:TO-252-2 | ~
21 | 1 | R1 | 412k | Device:R | Resistor_SMD:R_0805_2012Metric | ~
22 | 1 | R2 | 80.6k | Device:R | Resistor_SMD:R_0805_2012Metric | ~
23 | 1 | R3 | 0.003/1W | Device:R | Resistor_SMD:R_1206_3216Metric | ~
24 | 1 | R4 | 12k | Device:R | Resistor_SMD:R_0805_2012Metric | ~
25 | 1 | R5 | 309k | Device:R | Resistor_SMD:R_0805_2012Metric | ~
26 | 3 | R6, R8, R10 | 10k | Device:R | Resistor_SMD:R_0805_2012Metric | ~
27 | 1 | R7 | RIS | Device:R | Resistor_SMD:R_1206_3216Metric | ~
28 | 1 | R9 | FB3 | Device:R | Resistor_SMD:R_0805_2012Metric | ~
29 | 1 | R11 | 301 | Device:R | Resistor_SMD:R_0805_2012Metric | ~
30 | 1 | R12 | 0 | Device:R | Resistor_SMD:R_1206_3216Metric | ~
31 | 1 | RV1 | V27ZA2P | Device:Varistor | Varistor:RV_Disc_D12mm_W4.2mm_P7.5mm | ~
32 | 1 | RV2 | 20k | Device:R_POT | Potentiometer_THT:Potentiometer_Bourns_3296W_Vertical
33 | 1 | U1 | LTC4359-MS8 | Power_Management:LTC4359-MS8 | Package_SO:MSOP-8_3x3mm_P0.65mm | https://www.analog.com/media/en/technical-documentation/data-sheets/ltc4359.pdf
34 | 1 | U2 | LT8392 | t-top:LT8392 | Package_SO:TSSOP-28-1EP_4.4x9.7mm_P0.65mm

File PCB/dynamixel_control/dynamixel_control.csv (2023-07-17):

Source: | /home/marc-antoine/Bureau/Maitrîse/t-top_ws/src/t-top/PCB/dynamixel_control/dynamixel_control.kicad_sch
Date: | lun 17 avr 2023 12:57:41
Tool: | Eeschema 6.0.11-2627ca5db0~126~ubuntu20.04.1
Generator: | /usr/share/kicad/plugins/bom_csv_grouped_by_value.py
Component Count: | 53
Individual Components:
Item | Qty | Reference(s) | Value | LibPart | Footprint | Datasheet
 |  | C1 | 10µF/25V | Device:C | Capacitor_SMD:C_0805_2012Metric | ~
 |  | C2 | 4.7µF/25V | Device:C | Capacitor_SMD:C_0805_2012Metric | ~
 |  | C3 | 10µF/25V | Device:C | Capacitor_SMD:C_0805_2012Metric | ~
 |  | C4 | 0.1µF/25V | Device:C | Capacitor_SMD:C_0805_2012Metric | ~
 |  | C5 | 0.1µF/25V | Device:C | Capacitor_SMD:C_0805_2012Metric | ~
 |  | C6 | 10nF/25V | Device:C | Capacitor_SMD:C_0805_2012Metric | ~
 |  | C7 | 0.1µF/25V | Device:C | Capacitor_SMD:C_0805_2012Metric | ~
 |  | C8 | 0.1µF/25V | Device:C | Capacitor_SMD:C_0805_2012Metric | ~
 |  | C9 | 0.1µF/25V | Device:C | Capacitor_SMD:C_0805_2012Metric | ~
 |  | C10 | 0.1µF/25V | Device:C | Capacitor_SMD:C_0805_2012Metric | ~
 |  | C11 | 0.1µF/25V | Device:C | Capacitor_SMD:C_0805_2012Metric | ~
 |  | C12 | 2.2µF/25V | Device:C | Capacitor_SMD:C_0805_2012Metric | ~
 |  | C13 | 0.1µF/25V | Device:C | Capacitor_SMD:C_0805_2012Metric | ~
 |  | C14 | 10µF/25V | Device:C | Capacitor_SMD:C_0805_2012Metric | ~
 |  | C15 | 0.1µF/25V | Device:C | Capacitor_SMD:C_0805_2012Metric | ~
 |  | C18 | 0.1µF/25V | Device:C | Capacitor_SMD:C_0805_2012Metric | ~
 |  | C19 | 0.1µF/25V | Device:C | Capacitor_SMD:C_0805_2012Metric | ~
 |  | C22 | 0.1µF/25V | Device:C | Capacitor_SMD:C_0805_2012Metric | ~
 |  | C23 | 0.1µF/25V | Device:C | Capacitor_SMD:C_0805_2012Metric | ~
 |  | C25 | 2.2µF/25V | Device:C | Capacitor_SMD:C_0805_2012Metric | ~
 |  | J1 | 12V | Connector:Conn_01x02_Male | t-top:t-connector | ~
 |  | J2 | RS232 | Connector:Conn_01x03_Male | Connector_JST:JST_PH_S3B-PH-K_1x03_P2.00mm_Horizontal | ~
 |  | J6 | Debug Uart | Connector:Conn_01x03_Male | Connector_PinHeader_1.27mm:PinHeader_1x03_P1.27mm_Vertical | ~
 |  | J8 | Dynamixel TTL | Connector:Conn_01x03_Male | t-top:25SH-C-03-TS | ~
 |  | J11 | Dynamixel TTL | Connector:Conn_01x03_Male | t-top:25SH-C-03-TS | ~
 |  | J12 | Dynamixel TTL | Connector:Conn_01x03_Male | t-top:25SH-C-03-TS | ~
 |  | L1 | 12µH (RLS-126) | Device:L | Inductor_SMD:L_1812_4532Metric | ~
 |  | L2 | 12µH (RLS-126) | Device:L | Inductor_SMD:L_1812_4532Metric | ~
 |  | Q2 | IPD068P03L3GATMA1 | Device:Q_PMOS_GDS | Package_TO_SOT_SMD:TO-252-2 | ~
 |  | Q3 | T2N7002AK | Device:Q_NMOS_GSD | Package_TO_SOT_SMD:SOT-23 | ~
 |  | R1 | 10k | Device:R | Resistor_SMD:R_0805_2012Metric | ~
 |  | R2 | 10k | Device:R | Resistor_SMD:R_0805_2012Metric | ~
 |  | R3 | 10k | Device:R | Resistor_SMD:R_0805_2012Metric | ~
 |  | R4 | 0 | Device:R | Resistor_SMD:R_0805_2012Metric | ~
 |  | R7 | 2.2k | Device:R | Resistor_SMD:R_0805_2012Metric | ~
 |  | R8 | 2.2k | Device:R | Resistor_SMD:R_0805_2012Metric | ~
 |  | R9 | NI | Device:R | Resistor_SMD:R_0805_2012Metric | ~
 |  | R10 | 0 | Device:R | Resistor_SMD:R_0805_2012Metric | ~
 |  | R11 | 0 | Device:R | Resistor_SMD:R_0805_2012Metric | ~
 |  | R12 | 10k | Device:R | Resistor_SMD:R_0805_2012Metric | ~
 |  | R14 | 47 | Device:R | Resistor_SMD:R_0805_2012Metric | ~
 |  | R15 | 100k | Device:R | Resistor_SMD:R_0805_2012Metric | ~
 |  | R16 | 100k | Device:R | Resistor_SMD:R_0805_2012Metric | ~
 |  | R17 | 825 | Device:R | Resistor_SMD:R_0805_2012Metric | ~
 |  | R18 | 100k | Device:R | Resistor_SMD:R_0805_2012Metric | ~
 |  | SW1 | LIMIT_SWITCH | Switch:SW_SPST | Connector_JST:JST_PH_B2B-PH-K_1x02_P2.00mm_Vertical | ~
 |  | U1 | R-78E5.0-0.5 | t-top:R-78E5.0-0.5 | t-top:R-78E-0.5
 |  | U2 | SN74AHC1G14 | t-top:SN74AHC1G14 | Package_TO_SOT_SMD:SOT-23-5 | https://www.ti.com/lit/ds/symlink/sn74ahc1g14.pdf
 |  | U4 | Teensy_4.0 | t-top:Teensy_4.0 | t-top:Teensy_4.0
 |  | U5 | SN65C3221E | t-top:SN65C3221E | Package_SO:TSSOP-16_4.4x5mm_P0.65mm
 |  | U6 | ICM-40627 | t-top:ICM-40627 | t-top:ICM-40627
 |  | U7 | SN74LV1T34 | t-top:SN74LV1T34 | Package_TO_SOT_SMD:SOT-23-5 | https://www.ti.com/lit/ds/symlink/sn74lv1t34.pdf
 |  | U8 | SN74LVC2G241 | t-top:SN74LVC2G241 | Package_SO:VSSOP-8_2.3x2mm_P0.5mm
Collated Components:
Item | Qty | Reference(s) | Value | LibPart | Footprint | Datasheet
1 | 3 | C1, C3, C14 | 10µF/25V | Device:C | Capacitor_SMD:C_0805_2012Metric | ~
2 | 1 | C2 | 4.7µF/25V | Device:C | Capacitor_SMD:C_0805_2012Metric | ~
3 | 13 | C4, C5, C7, C8, C9, C10, C11, C13, C15, C18, C19, C22, C23 | 0.1µF/25V | Device:C | Capacitor_SMD:C_0805_2012Metric | ~
4 | 1 | C6 | 10nF/25V | Device:C | Capacitor_SMD:C_0805_2012Metric | ~
5 | 2 | C12, C25 | 2.2µF/25V | Device:C | Capacitor_SMD:C_0805_2012Metric | ~
6 | 1 | J1 | 12V | Connector:Conn_01x02_Male | t-top:t-connector | ~
7 | 1 | J2 | RS232 | Connector:Conn_01x03_Male | Connector_JST:JST_PH_S3B-PH-K_1x03_P2.00mm_Horizontal | ~
8 | 1 | J6 | Debug Uart | Connector:Conn_01x03_Male | Connector_PinHeader_1.27mm:PinHeader_1x03_P1.27mm_Vertical | ~
9 | 3 | J8, J11, J12 | Dynamixel TTL | Connector:Conn_01x03_Male | t-top:25SH-C-03-TS | ~
10 | 2 | L1, L2 | 12µH (RLS-126) | Device:L | Inductor_SMD:L_1812_4532Metric | ~
11 | 1 | Q2 | IPD068P03L3GATMA1 | Device:Q_PMOS_GDS | Package_TO_SOT_SMD:TO-252-2 | ~
12 | 1 | Q3 | T2N7002AK | Device:Q_NMOS_GSD | Package_TO_SOT_SMD:SOT-23 | ~
13 | 4 | R1, R2, R3, R12 | 10k | Device:R | Resistor_SMD:R_0805_2012Metric | ~
14 | 3 | R4, R10, R11 | 0 | Device:R | Resistor_SMD:R_0805_2012Metric | ~
15 | 2 | R7, R8 | 2.2k | Device:R | Resistor_SMD:R_0805_2012Metric | ~
16 | 1 | R9 | NI | Device:R | Resistor_SMD:R_0805_2012Metric | ~
17 | 1 | R14 | 47 | Device:R | Resistor_SMD:R_0805_2012Metric | ~
18 | 3 | R15, R16, R18 | 100k | Device:R | Resistor_SMD:R_0805_2012Metric | ~
19 | 1 | R17 | 825 | Device:R | Resistor_SMD:R_0805_2012Metric | ~
20 | 1 | SW1 | LIMIT_SWITCH | Switch:SW_SPST | Connector_JST:JST_PH_B2B-PH-K_1x02_P2.00mm_Vertical | ~
21 | 1 | U1 | R-78E5.0-0.5 | t-top:R-78E5.0-0.5 | t-top:R-78E-0.5
22 | 1 | U2 | SN74AHC1G14 | t-top:SN74AHC1G14 | Package_TO_SOT_SMD:SOT-23-5 | https://www.ti.com/lit/ds/symlink/sn74ahc1g14.pdf
23 | 1 | U4 | Teensy_4.0 | t-top:Teensy_4.0 | t-top:Teensy_4.0
24 | 1 | U5 | SN65C3221E | t-top:SN65C3221E | Package_SO:TSSOP-16_4.4x5mm_P0.65mm
25 | 1 | U6 | ICM-40627 | t-top:ICM-40627 | t-top:ICM-40627
26 | 1 | U7 | SN74LV1T34 | t-top:SN74LV1T34 | Package_TO_SOT_SMD:SOT-23-5 | https://www.ti.com/lit/ds/symlink/sn74lv1t34.pdf
27 | 1 | U8 | SN74LVC2G241 | t-top:SN74LVC2G241 | Package_SO:VSSOP-8_2.3x2mm_P0.5mm

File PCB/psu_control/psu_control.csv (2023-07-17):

Source: | /home/marc-antoine/Bureau/Maitrîse/t-top_ws/src/t-top/PCB/psu_control/psu_control.kicad_sch
Date: | lun 17 avr 2023 11:36:40
Tool: | Eeschema 6.0.11-2627ca5db0~126~ubuntu20.04.1
Generator: | /usr/share/kicad/plugins/bom_csv_grouped_by_value.py
Component Count: | 115
Individual Components:
Item | Qty | Reference(s) | Value | LibPart | Footprint | Datasheet
 |  | C1 | 0.1µF/25V | Device:C | Capacitor_SMD:C_0805_2012Metric | ~
 |  | C2 | 2.2µF/25V | Device:C | Capacitor_SMD:C_0805_2012Metric | ~
 |  | C3 | 1µF/10V | Device:C | Capacitor_SMD:C_0805_2012Metric | ~
 |  | C4 | 22μF/10V | Device:C | Capacitor_SMD:C_0805_2012Metric | ~
 |  | C5 | 100µF/35V | Device:C_Polarized | Capacitor_THT:CP_Radial_D6.3mm_P2.50mm | ~
 |  | C6 | 680µF/35V | Device:C_Polarized | Capacitor_THT:CP_Radial_D10.0mm_P5.00mm | ~
 |  | C7 | 0.1µF/25V | Device:C | Capacitor_SMD:C_0805_2012Metric | ~
 |  | C8 | 0.1µF/25V | Device:C | Capacitor_SMD:C_0805_2012Metric | ~
 |  | C9 | 100µF/35V | Device:C_Polarized | Capacitor_THT:CP_Radial_D6.3mm_P2.50mm | ~
 |  | C10 | 10µF/25V | Device:C | Capacitor_SMD:C_0805_2012Metric | ~
 |  | C11 | 0.1µF/25V | Device:C | Capacitor_SMD:C_0805_2012Metric | ~
 |  | C12 | 0.1µF/25V | Device:C | Capacitor_SMD:C_0805_2012Metric | ~
 |  | C13 | 0.1µF/25V | Device:C | Capacitor_SMD:C_0805_2012Metric | ~
 |  | C14 | 0.1µF/25V | Device:C | Capacitor_SMD:C_0805_2012Metric | ~
 |  | C15 | 0.1µF/25V | Device:C | Capacitor_SMD:C_0805_2012Metric | ~
 |  | C16 | 0.1µF/25V | Device:C | Capacitor_SMD:C_0805_2012Metric | ~
 |  | C17 | 0.1µF/25V | Device:C | Capacitor_SMD:C_0805_2012Metric | ~
 |  | C18 | 0.1µF/25V | Device:C | Capacitor_SMD:C_0805_2012Metric | ~
 |  | C19 | 0.1µF/25V | Device:C | Capacitor_SMD:C_0805_2012Metric | ~
 |  | C20 | 0.1µF/25V | Device:C | Capacitor_SMD:C_0805_2012Metric | ~
 |  | C21 | 0.1µF/25V | Device:C | Capacitor_SMD:C_0805_2012Metric | ~
 |  | C22 | 0.1µF/25V | Device:C | Capacitor_SMD:C_0805_2012Metric | ~
 |  | C23 | 100µF/35V | Device:C_Polarized | Capacitor_THT:CP_Radial_D6.3mm_P2.50mm | ~
 |  | C24 | 10µF/25V | Device:C | Capacitor_SMD:C_0805_2012Metric | ~
 |  | C25 | 0.1µF/25V | Device:C | Capacitor_SMD:C_0805_2012Metric | ~
 |  | C26 | 0.1µF/25V | Device:C | Capacitor_SMD:C_0805_2012Metric | ~
 |  | C27 | 0.1µF/25V | Device:C | Capacitor_SMD:C_0805_2012Metric | ~
 |  | C28 | 0.1µF/25V | Device:C | Capacitor_SMD:C_0805_2012Metric | ~
 |  | C29 | 0.1µF/25V | Device:C | Capacitor_SMD:C_0805_2012Metric | ~
 |  | C30 | 0.1µF/25V | Device:C | Capacitor_SMD:C_0805_2012Metric | ~
 |  | C31 | 22μF/10V | Device:C | Capacitor_SMD:C_0805_2012Metric | ~
 |  | D1 | DSS16U | Device:D_Schottky | Diode_SMD:D_SOD-123F | ~
 |  | D2 | DSS16U | Device:D_Schottky | Diode_SMD:D_SOD-123F | ~
 |  | D3 | DSS16U | Device:D_Schottky | Diode_SMD:D_SOD-123F | ~
 |  | D4 | White | Device:LED | Connector_JST:JST_PH_B2B-PH-K_1x02_P2.00mm_Vertical | ~
 |  | D5 | White | Device:LED | Connector_JST:JST_PH_B2B-PH-K_1x02_P2.00mm_Vertical | ~
 |  | D6 | SMAJ9.0A-13-F | Device:D | Diode_SMD:D_SMA | ~
 |  | F1 | 10A Slow Blow | Device:Fuse | t-top:M205_FUSE | ~
 |  | J1 | Vin (10-25V) | Connector:Conn_01x02_Male | t-top:OSTTA020161 | ~
 |  | J2 | Vout (10-25V) | Connector:Conn_01x02_Male | t-top:OSTTA020161 | ~
 |  | J4 | Vout (10-25V) | Connector:Conn_01x02_Male | t-top:OSTTA020161 | ~
 |  | J6 | LED Strip | Connector:Conn_01x03_Male | Connector_JST:JST_XH_B3B-XH-A_1x03_P2.50mm_Vertical | ~
 |  | J7 | Amplifier 2 I2C | Connector:Conn_01x03_Male | Connector_JST:JST_PH_B3B-PH-K_1x03_P2.00mm_Vertical | ~
 |  | J8 | Amplifier 1 I2C | Connector:Conn_01x03_Male | Connector_JST:JST_PH_B3B-PH-K_1x03_P2.00mm_Vertical | ~
 |  | J11 | Light Sensor Front | Connector:Conn_01x03_Male | Connector_JST:JST_PH_B3B-PH-K_1x03_P2.00mm_Vertical | ~
 |  | J12 | Light Sensor Left | Connector:Conn_01x03_Male | Connector_JST:JST_PH_B3B-PH-K_1x03_P2.00mm_Vertical | ~
 |  | J13 | Light Sensor Back | Connector:Conn_01x03_Male | Connector_JST:JST_PH_B3B-PH-K_1x03_P2.00mm_Vertical | ~
 |  | J14 | Light Sensor Right | Connector:Conn_01x03_Male | Connector_JST:JST_PH_B3B-PH-K_1x03_P2.00mm_Vertical | ~
 |  | J15 | RRC-PMM240 | Connector:Conn_01x05_Male | Connector_JST:JST_PH_B5B-PH-K_1x05_P2.00mm_Vertical | ~
 |  | J16 | RS232 | Connector:Conn_01x03_Male | Connector_JST:JST_PH_B3B-PH-K_1x03_P2.00mm_Vertical | ~
 |  | L1 | 22µH (NS12575T220MN) | Device:L_Ferrite | t-top:NS12575T220MN | ~
 |  | L2 | 22µH (NS12575T220MN) | Device:L_Ferrite | t-top:NS12575T220MN | ~
 |  | LS1 | CEM-1206S | Device:Speaker | t-top:WT-1205 | ~
 |  | M1 | Fan | t-top:Fan | Connector_JST:JST_PH_B2B-PH-K_1x02_P2.00mm_Vertical | ~
 |  | M2 | Fan | t-top:Fan | Connector_JST:JST_PH_B2B-PH-K_1x02_P2.00mm_Vertical | ~
 |  | Q2 | IPD068P03L3GATMA1 | Device:Q_PMOS_GDS | Package_TO_SOT_SMD:TO-252-2 | ~
 |  | Q3 | T2N7002AK | Device:Q_NMOS_GSD | Package_TO_SOT_SMD:SOT-23 | ~
 |  | Q4 | DMG9926USD | t-top:DMG9926USD | Package_SO:SOIC-8_3.9x4.9mm_P1.27mm
 |  | R3 | 2.2k | Device:R | Resistor_SMD:R_0805_2012Metric | ~
 |  | R4 | 2.2k | Device:R | Resistor_SMD:R_0805_2012Metric | ~
 |  | R5 | 100k | Device:R | Resistor_SMD:R_0805_2012Metric | ~
 |  | R6 | 100k | Device:R | Resistor_SMD:R_0805_2012Metric | ~
 |  | R7 | 0 | Device:R | Resistor_SMD:R_0805_2012Metric | ~
 |  | R8 | 0 | Device:R | Resistor_SMD:R_0805_2012Metric | ~
 |  | R9 | 0 | Device:R | Resistor_SMD:R_0805_2012Metric | ~
 |  | R10 | 0 | Device:R | Resistor_SMD:R_0805_2012Metric | ~
 |  | R11 | 10 | Device:R | Resistor_SMD:R_0805_2012Metric | ~
 |  | R12 | 10 | Device:R | Resistor_SMD:R_0805_2012Metric | ~
 |  | R13 | 100k | Device:R | Resistor_SMD:R_0805_2012Metric | ~
 |  | R14 | 0.004 | Device:R | Resistor_SMD:R_1206_3216Metric | ~
 |  | R15 | 10k | Device:R | Resistor_SMD:R_0805_2012Metric | ~
 |  | R16 | NI | Device:R | Resistor_SMD:R_0805_2012Metric | ~
 |  | R17 | NI | Device:R | Resistor_SMD:R_0805_2012Metric | ~
 |  | R18 | 10k | Device:R | Resistor_SMD:R_0805_2012Metric | ~
 |  | R19 | NI | Device:R | Resistor_SMD:R_0805_2012Metric | ~
 |  | R20 | NI | Device:R | Resistor_SMD:R_0805_2012Metric | ~
 |  | R21 | 698 | Device:R | Resistor_SMD:R_0805_2012Metric | ~
 |  | R22 | 698 | Device:R | Resistor_SMD:R_0805_2012Metric | ~
 |  | R23 | 100k | Device:R | Resistor_SMD:R_0805_2012Metric | ~
 |  | R24 | 100k | Device:R | Resistor_SMD:R_0805_2012Metric | ~
 |  | R25 | 10k | Device:R | Resistor_SMD:R_0805_2012Metric | ~
 |  | R26 | 10k | Device:R | Resistor_SMD:R_0805_2012Metric | ~
 |  | R27 | 10k | Device:R | Resistor_SMD:R_0805_2012Metric | ~
 |  | R28 | 10k | Device:R | Resistor_SMD:R_0805_2012Metric | ~
 |  | R29 | 10k | Device:R | Resistor_SMD:R_0805_2012Metric | ~
 |  | R30 | 10k | Device:R | Resistor_SMD:R_0805_2012Metric | ~
 |  | R31 | 10k | Device:R | Resistor_SMD:R_0805_2012Metric | ~
 |  | R32 | 10k | Device:R | Resistor_SMD:R_0805_2012Metric | ~
 |  | R33 | 10k | Device:R | Resistor_SMD:R_0805_2012Metric | ~
 |  | R34 | 10k | Device:R | Resistor_SMD:R_0805_2012Metric | ~
 |  | R35 | 10k | Device:R | Resistor_SMD:R_0805_2012Metric | ~
 |  | R36 | 10k | Device:R | Resistor_SMD:R_0805_2012Metric | ~
 |  | R37 | 63.4 | Device:R | Resistor_SMD:R_0805_2012Metric | ~
 |  | R38 | 63.4 | Device:R | Resistor_SMD:R_0805_2012Metric | ~
 |  | R39 | 698 | Device:R | Resistor_SMD:R_0805_2012Metric | ~
 |  | R40 | 2.2k | Device:R | Resistor_SMD:R_0805_2012Metric | ~
 |  | R41 | 2.2k | Device:R | Resistor_SMD:R_0805_2012Metric | ~
 |  | R42 | 47 | Device:R | Resistor_SMD:R_0805_2012Metric | ~
 |  | R43 | 0 | Device:R | Resistor_SMD:R_1206_3216Metric | ~
 |  | R44 | 0 | Device:R | Resistor_SMD:R_1206_3216Metric | ~
 |  | SW1 | Non-Momentary DPST | Switch:SW_DPST_x2 | Connector_JST:JST_PH_B4B-PH-K_1x04_P2.00mm_Vertical | ~
 |  | SW2 | BUTTON | Switch:SW_SPST | Connector_JST:JST_PH_B2B-PH-K_1x02_P2.00mm_Vertical | ~
 |  | SW3 | BUTTON | Switch:SW_SPST | Connector_JST:JST_PH_B2B-PH-K_1x02_P2.00mm_Vertical | ~
 |  | SW4 | BUTTON | Switch:SW_SPST | Connector_JST:JST_PH_B2B-PH-K_1x02_P2.00mm_Vertical | ~
 |  | SW5 | BUTTON | Switch:SW_SPST | Connector_JST:JST_PH_B2B-PH-K_1x02_P2.00mm_Vertical | ~
 |  | SW6 | BUTTON | Switch:SW_SPST | Connector_JST:JST_PH_B2B-PH-K_1x02_P2.00mm_Vertical | ~
 |  | TH1 | 10k | Device:Thermistor | Connector_JST:JST_PH_B2B-PH-K_1x02_P2.00mm_Vertical | ~
 |  | TH2 | 10k | Device:Thermistor | Resistor_SMD:R_0805_2012Metric | ~
 |  | U2 | Teensy_LC | t-top:Teensy_LC | t-top:Teensy_LC
 |  | U3 | INA220 | t-top:INA220 | Package_SO:VSSOP-10_3x3mm_P0.5mm
 |  | U4 | K7805-3AR3 | t-top:K7805-3AR3 | t-top:K7805-3AR3
 |  | U5 | 74HC14 | t-top:74HC14 | Package_SO:TSSOP-14_4.4x5mm_P0.65mm | http://www.ti.com/lit/gpn/sn74HC14
 |  | U6 | SN74LV1T34 | t-top:SN74LV1T34 | Package_TO_SOT_SMD:SOT-23-5 | https://www.ti.com/lit/ds/symlink/sn74lv1t34.pdf
 |  | U7 | SN65C3221E | t-top:SN65C3221E | Package_SO:TSSOP-16_4.4x5mm_P0.65mm
 |  | U8 | 74LVC2G34 | t-top:74LVC2G34 | Package_SO:TSOP-6_1.65x3.05mm_P0.95mm | https://assets.nexperia.com/documents/data-sheet/74LVC2G34.pdf
Collated Components:
Item | Qty | Reference(s) | Value | LibPart | Footprint | Datasheet
1 | 21 | C1, C7, C8, C11, C12, C13, C14, C15, C16, C17, C18, C19, C20, C21, C22, C25, C26, C27, C28, C29, C30 | 0.1µF/25V | Device:C | Capacitor_SMD:C_0805_2012Metric | ~
2 | 1 | C2 | 2.2µF/25V | Device:C | Capacitor_SMD:C_0805_2012Metric | ~
3 | 1 | C3 | 1µF/10V | Device:C | Capacitor_SMD:C_0805_2012Metric | ~
4 | 2 | C4, C31 | 22μF/10V | Device:C | Capacitor_SMD:C_0805_2012Metric | ~
5 | 3 | C5, C9, C23 | 100µF/35V | Device:C_Polarized | Capacitor_THT:CP_Radial_D6.3mm_P2.50mm | ~
6 | 1 | C6 | 680µF/35V | Device:C_Polarized | Capacitor_THT:CP_Radial_D10.0mm_P5.00mm | ~
7 | 2 | C10, C24 | 10µF/25V | Device:C | Capacitor_SMD:C_0805_2012Metric | ~
8 | 3 | D1, D2, D3 | DSS16U | Device:D_Schottky | Diode_SMD:D_SOD-123F | ~
9 | 2 | D4, D5 | White | Device:LED | Connector_JST:JST_PH_B2B-PH-K_1x02_P2.00mm_Vertical | ~
10 | 1 | D6 | SMAJ9.0A-13-F | Device:D | Diode_SMD:D_SMA | ~
11 | 1 | F1 | 10A Slow Blow | Device:Fuse | t-top:M205_FUSE | ~
12 | 1 | J1 | Vin (10-25V) | Connector:Conn_01x02_Male | t-top:OSTTA020161 | ~
13 | 2 | J2, J4 | Vout (10-25V) | Connector:Conn_01x02_Male | t-top:OSTTA020161 | ~
14 | 1 | J6 | LED Strip | Connector:Conn_01x03_Male | Connector_JST:JST_XH_B3B-XH-A_1x03_P2.50mm_Vertical | ~
15 | 1 | J7 | Amplifier 2 I2C | Connector:Conn_01x03_Male | Connector_JST:JST_PH_B3B-PH-K_1x03_P2.00mm_Vertical | ~
16 | 1 | J8 | Amplifier 1 I2C | Connector:Conn_01x03_Male | Connector_JST:JST_PH_B3B-PH-K_1x03_P2.00mm_Vertical | ~
17 | 1 | J11 | Light Sensor Front | Connector:Conn_01x03_Male | Connector_JST:JST_PH_B3B-PH-K_1x03_P2.00mm_Vertical | ~
18 | 1 | J12 | Light Sensor Left | Connector:Conn_01x03_Male | Connector_JST:JST_PH_B3B-PH-K_1x03_P2.00mm_Vertical | ~
19 | 1 | J13 | Light Sensor Back | Connector:Conn_01x03_Male | Connector_JST:JST_PH_B3B-PH-K_1x03_P2.00mm_Vertical | ~
20 | 1 | J14 | Light Sensor Right | Connector:Conn_01x03_Male | Connector_JST:JST_PH_B3B-PH-K_1x03_P2.00mm_Vertical | ~
21 | 1 | J15 | RRC-PMM240 | Connector:Conn_01x05_Male | Connector_JST:JST_PH_B5B-PH-K_1x05_P2.00mm_Vertical | ~
22 | 1 | J16 | RS232 | Connector:Conn_01x03_Male | Connector_JST:JST_PH_B3B-PH-K_1x03_P2.00mm_Vertical | ~
23 | 2 | L1, L2 | 22µH (NS12575T220MN) | Device:L_Ferrite | t-top:NS12575T220MN | ~
24 | 1 | LS1 | CEM-1206S | Device:Speaker | t-top:WT-1205 | ~
25 | 2 | M1, M2 | Fan | t-top:Fan | Connector_JST:JST_PH_B2B-PH-K_1x02_P2.00mm_Vertical | ~
26 | 1 | Q2 | IPD068P03L3GATMA1 | Device:Q_PMOS_GDS | Package_TO_SOT_SMD:TO-252-2 | ~
27 | 1 | Q3 | T2N7002AK | Device:Q_NMOS_GSD | Package_TO_SOT_SMD:SOT-23 | ~
28 | 1 | Q4 | DMG9926USD | t-top:DMG9926USD | Package_SO:SOIC-8_3.9x4.9mm_P1.27mm
29 | 4 | R3, R4, R40, R41 | 2.2k | Device:R | Resistor_SMD:R_0805_2012Metric | ~
30 | 5 | R5, R6, R13, R23, R24 | 100k | Device:R | Resistor_SMD:R_0805_2012Metric | ~
31 | 4 | R7, R8, R9, R10 | 0 | Device:R | Resistor_SMD:R_0805_2012Metric | ~
32 | 2 | R11, R12 | 10 | Device:R | Resistor_SMD:R_0805_2012Metric | ~
33 | 1 | R14 | 0.004 | Device:R | Resistor_SMD:R_1206_3216Metric | ~
34 | 14 | R15, R18, R25, R26, R27, R28, R29, R30, R31, R32, R33, R34, R35, R36 | 10k | Device:R | Resistor_SMD:R_0805_2012Metric | ~
35 | 4 | R16, R17, R19, R20 | NI | Device:R | Resistor_SMD:R_0805_2012Metric | ~
36 | 3 | R21, R22, R39 | 698 | Device:R | Resistor_SMD:R_0805_2012Metric | ~
37 | 2 | R37, R38 | 63.4 | Device:R | Resistor_SMD:R_0805_2012Metric | ~
38 | 1 | R42 | 47 | Device:R | Resistor_SMD:R_0805_2012Metric | ~
39 | 2 | R43, R44 | 0 | Device:R | Resistor_SMD:R_1206_3216Metric | ~
40 | 1 | SW1 | Non-Momentary DPST | Switch:SW_DPST_x2 | Connector_JST:JST_PH_B4B-PH-K_1x04_P2.00mm_Vertical | ~
41 | 5 | SW2, SW3, SW4, SW5, SW6 | BUTTON | Switch:SW_SPST | Connector_JST:JST_PH_B2B-PH-K_1x02_P2.00mm_Vertical | ~
42 | 1 | TH1 | 10k | Device:Thermistor | Connector_JST:JST_PH_B2B-PH-K_1x02_P2.00mm_Vertical | ~
43 | 1 | TH2 | 10k | Device:Thermistor | Resistor_SMD:R_0805_2012Metric | ~
44 | 1 | U2 | Teensy_LC | t-top:Teensy_LC | t-top:Teensy_LC
45 | 1 | U3 | INA220 | t-top:INA220 | Package_SO:VSSOP-10_3x3mm_P0.5mm
46 | 1 | U4 | K7805-3AR3 | t-top:K7805-3AR3 | t-top:K7805-3AR3
47 | 1 | U5 | 74HC14 | t-top:74HC14 | Package_SO:TSSOP-14_4.4x5mm_P0.65mm | http://www.ti.com/lit/gpn/sn74HC14
48 | 1 | U6 | SN74LV1T34 | t-top:SN74LV1T34 | Package_TO_SOT_SMD:SOT-23-5 | https://www.ti.com/lit/ds/symlink/sn74lv1t34.pdf
49 | 1 | U7 | SN65C3221E | t-top:SN65C3221E | Package_SO:TSSOP-16_4.4x5mm_P0.65mm
50 | 1 | U8 | 74LVC2G34 | t-top:74LVC2G34 | Package_SO:TSOP-6_1.65x3.05mm_P0.95mm | https://assets.nexperia.com/documents/data-sheet/74LVC2G34.pdf

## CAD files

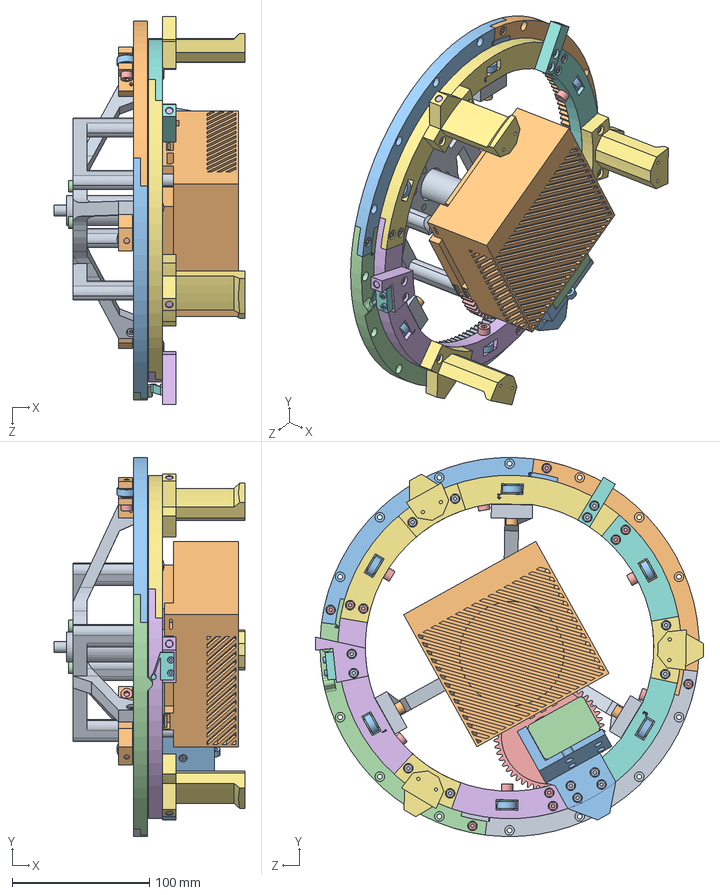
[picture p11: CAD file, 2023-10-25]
CAD/assemblies/torso bottom orin.SLDASM
138.9 x 275.9 x 282.4 mm
base gear 1
base gear 2
base gear 3
base gear 4
M3x6mm plastic x 10
torso bottom external 1
torso bottom external 2
torso bottom external 3
torso bottom internal orin
torso bottom holder x 3
605zz x 9
M5 washer x 18
M5x16mm socket x 6
limit switch bracket
stewart stand x 3
limit switch
slip ring (SNM220A-24)
Jetson AGX Orin
gear servo bracket
XL430-W250-T
torso bottom gear
M2.5x8mm plastic x 6
M2x12mm socket x 4
torso bottom magnet bracket
M3x12mm plastic x 26
M5x30mm socket x 3
M2.5x12mm plastic x 2
M5x10mm plastic x 3
M2.5x30mm socket x 4
magnet 5x1.6 x 6

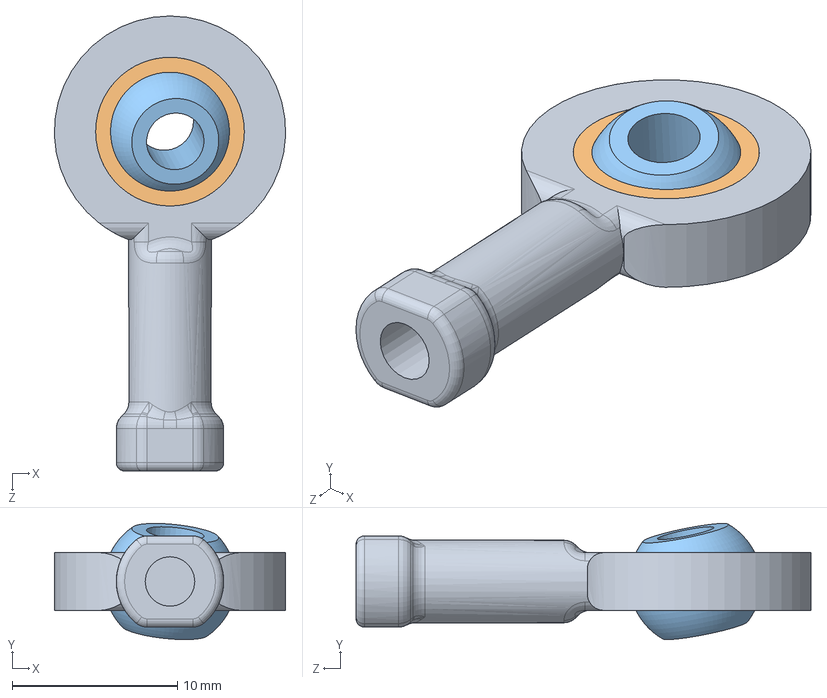
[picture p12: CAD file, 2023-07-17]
CAD/hardware/ball joint/ball joint.SLDASM
14.0 x 7.03 x 27.5 mm
ball joint body
ball joint liner
ball joint ball

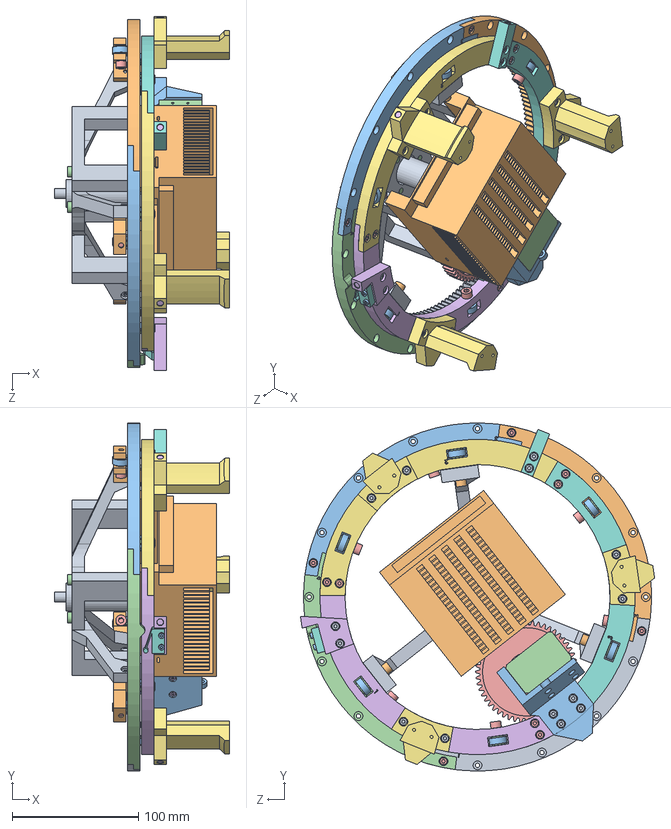
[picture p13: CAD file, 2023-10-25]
CAD/assemblies/torso bottom xavier.SLDASM
138.9 x 275.9 x 280.8 mm
base gear 1
base gear 2
base gear 3
base gear 4
M3x6mm plastic x 10
torso bottom external 1
torso bottom external 2
torso bottom external 3
torso bottom internal xavier
torso bottom holder x 3
605zz x 9
M5 washer x 18
M5x16mm socket x 6
limit switch bracket
stewart stand x 3
limit switch
slip ring (SNM220A-24)
Jetson AGX Xavier
gear servo bracket
XL430-W250-T
torso bottom gear
M2.5x8mm plastic x 6
M2x12mm socket x 4
torso bottom magnet bracket
M3x12mm plastic x 26
M5x30mm socket x 3
M2.5x12mm plastic x 2
M5x10mm plastic x 3
M3x55mm socket x 4
magnet 5x1.6 x 6

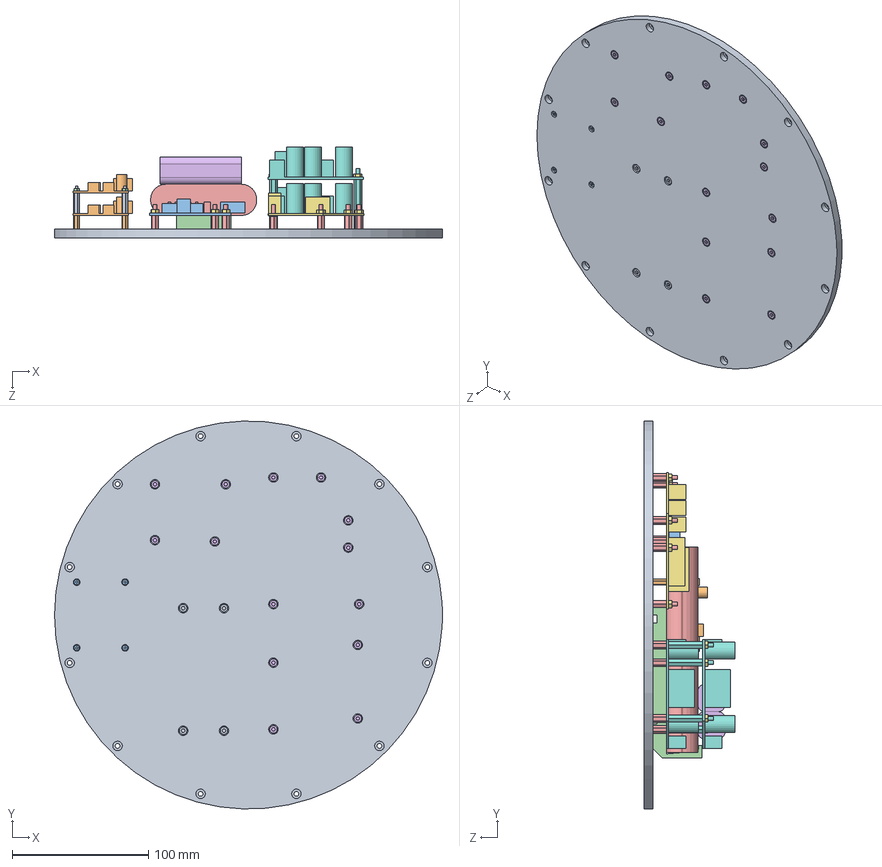
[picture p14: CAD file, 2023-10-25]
CAD/assemblies/base disk.SLDASM
285.0 x 284.9 x 66.6 mm
base disk
Adafruit MAX9744 x 2
Battery charger RRC-PMM240
battery holder
Battery RRC2054-2
ground loop noise isolator x 2
psu control
buck boost x 2
732-12936-ND x 4
732-12918-ND x 4
M2x8mm socket x 4
M2 nut x 4
36-24337-ND x 14
M3x5mm socket x 14
M3 nut x 14
36-24342-ND x 4
M3x8mm plastic x 4

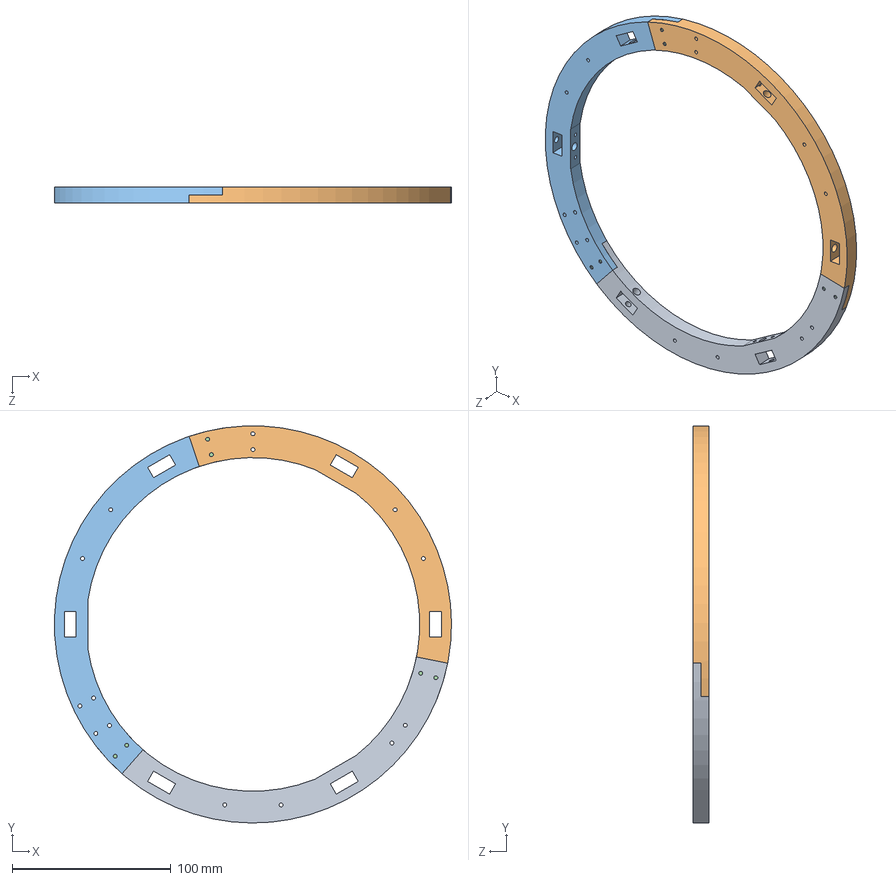
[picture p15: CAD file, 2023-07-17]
CAD/assemblies/torso bottom external.SLDASM
249.9 x 249.9 x 10.0 mm
torso bottom external 1
torso bottom external 2
torso bottom external 3
M3x6mm plastic x 6

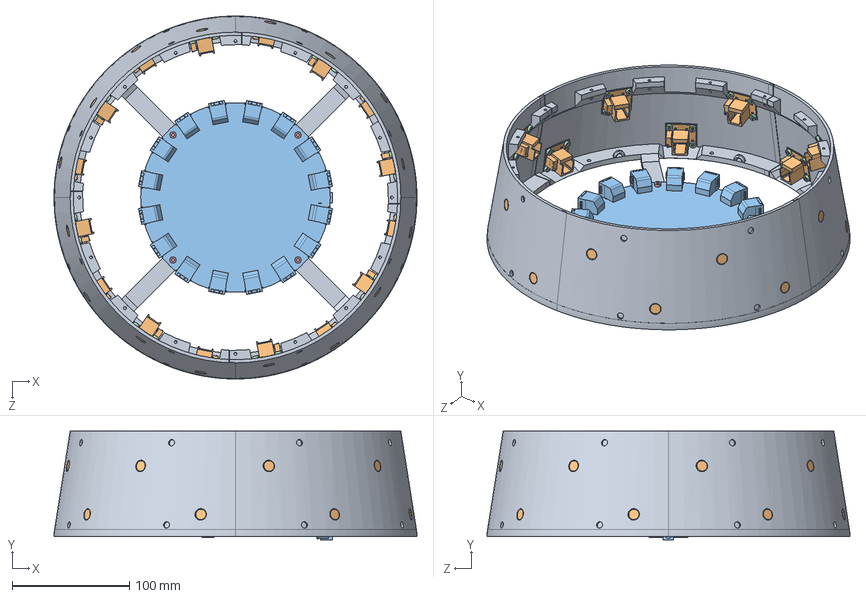
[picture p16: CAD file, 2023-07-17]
CAD/assemblies/base mic.SLDASM
310.0 x 92.8 x 310.0 mm
base mic x 4
8SoundsUSB Mic x 16
16SoundsUSB
M3x5mm plastic x 64
M3x8mm plastic x 4

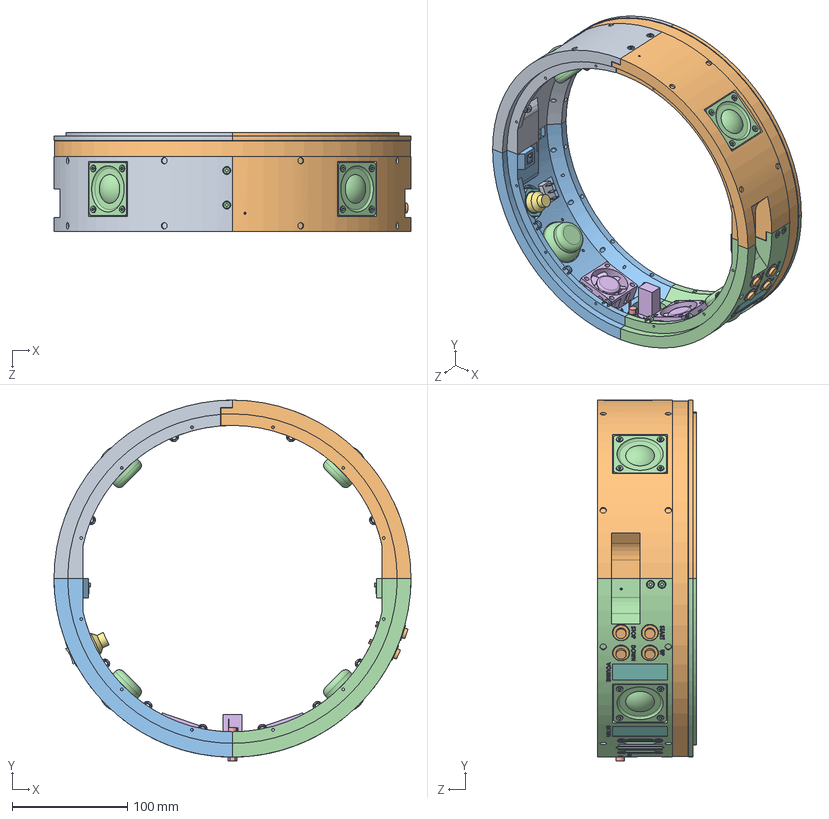
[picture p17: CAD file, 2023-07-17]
CAD/assemblies/base audio.SLDASM
310.0 x 313.3 x 86.0 mm
base audio front left
base audio front right
base audio back left
base audio back right
SC2073-ND
RJ45 connector
Micro USB B (Adafruit 4217)
Micro USB B nut (Adafruit 4217)
switch
button x 4
button nut x 3
Dayton Audio DMA45-8 x 4
LED 5mm x 2
Noctua NF-A4X20 x 2
LED level x 2
LED level diffuser x 2
LED strip
LED strip diffuser (round)
light sensor x 4
M3x8mm plastic x 22
fan screw x 8
dewel pin 0.125in 0.5in x 2
M2x5mm plastic x 4

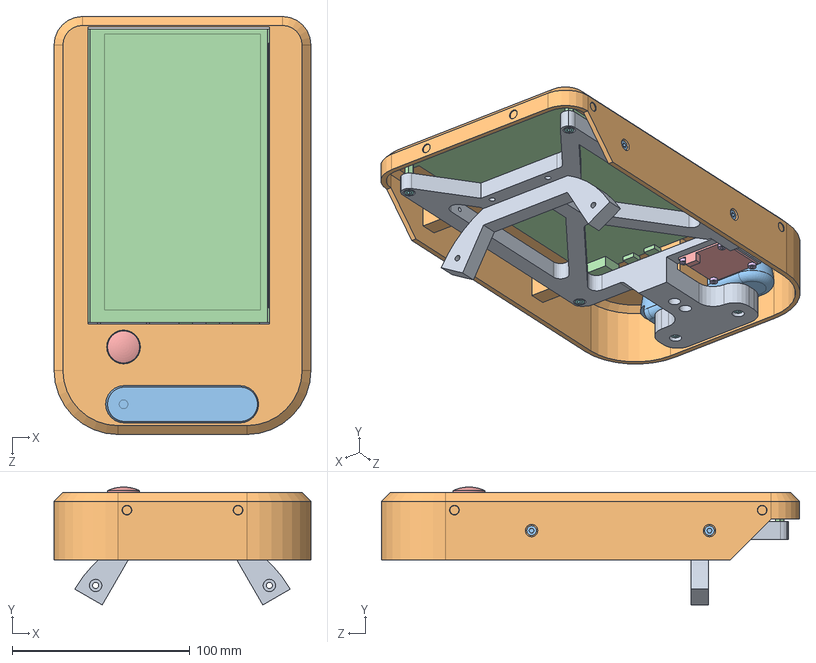
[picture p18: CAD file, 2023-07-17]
CAD/assemblies/head.SLDASM
144.4 x 66.3 x 235.0 mm
head
head cable protector
Intel RealSense D435i
screen
wide angle camera
M2.5x5mm plastic x 4
M3x12mm plastic x 2
M3x10mm socket x 6
M3x5mm socket x 4
magnet 5x1.6 x 8
M3x8mm plastic x 4

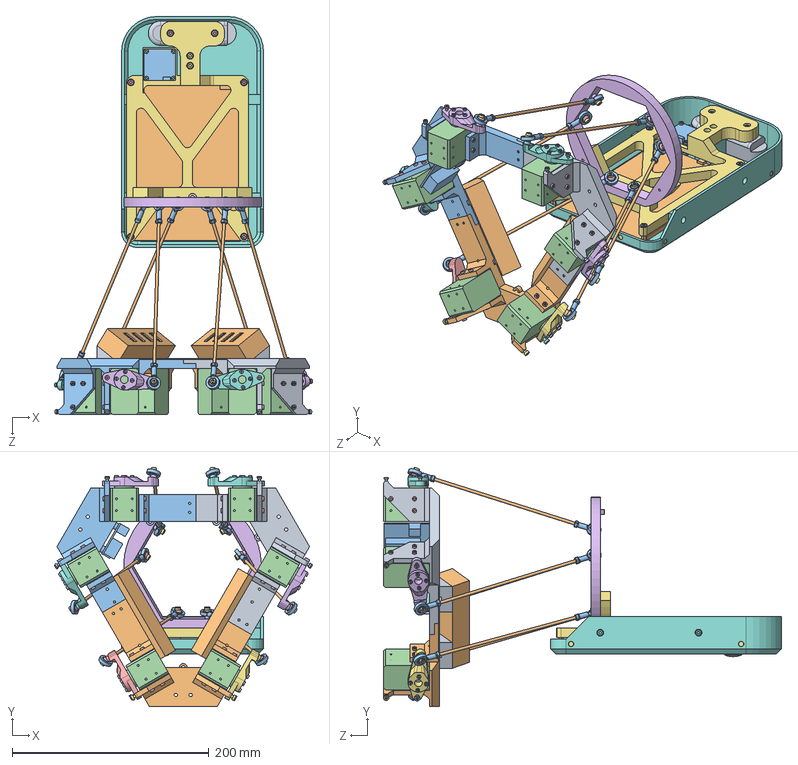
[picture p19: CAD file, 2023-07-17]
CAD/assemblies/stewart.SLDASM
262.7 x 243.6 x 404.8 mm
stewart bottom 1
stewart bottom 2
stewart bottom 3
XL430-W250-T x 6
stewart horn left M3
stewart horn left M2.5 x 2
stewart horn right M3
stewart horn right M2.5 x 2
USB hub stand x 4
Anker USB-c hub (4 ports) x 2
dynamixel control
M3x6mm plastic x 6
M2.5x8mm plastic x 46
M2x12mm socket x 24
M3x12mm plastic x 28
M3x8mm plastic x 8
M2.5x12mm plastic x 4
stewart rod x 6
ball joint body x 12
ball joint liner x 12
ball joint ball x 12
stewart top
head
head cable protector
Intel RealSense D435i
screen
wide angle camera
M2.5x5mm plastic x 4
M3x10mm socket x 6
M3x5mm socket x 4
magnet 5x1.6 x 8

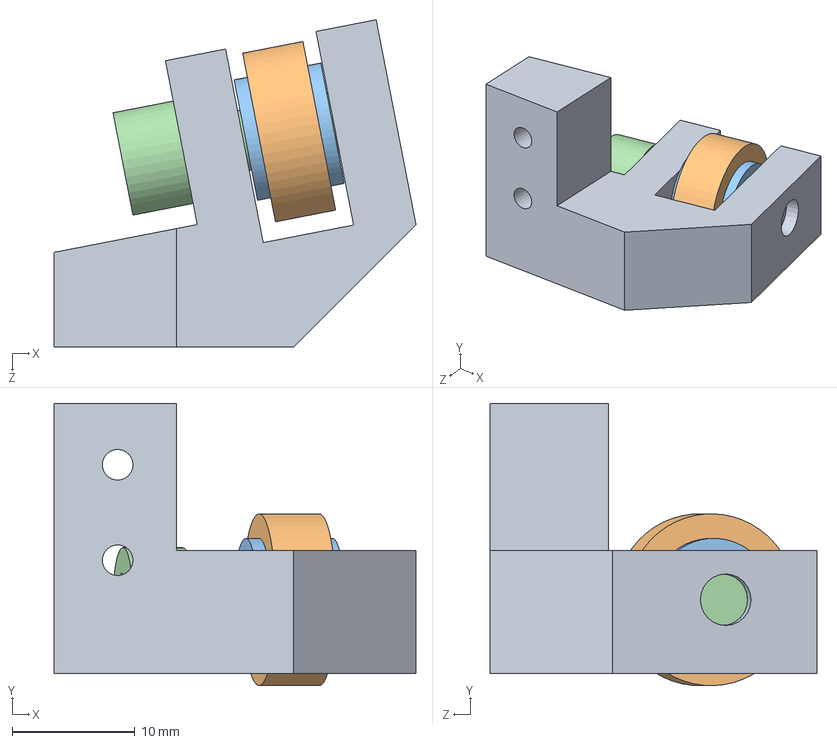
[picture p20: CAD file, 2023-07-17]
CAD/assemblies/torso bottom holder.SLDASM
29.5 x 23.0 x 26.7 mm
torso bottom holder
605zz
M5 washer x 2
M5x16mm socket

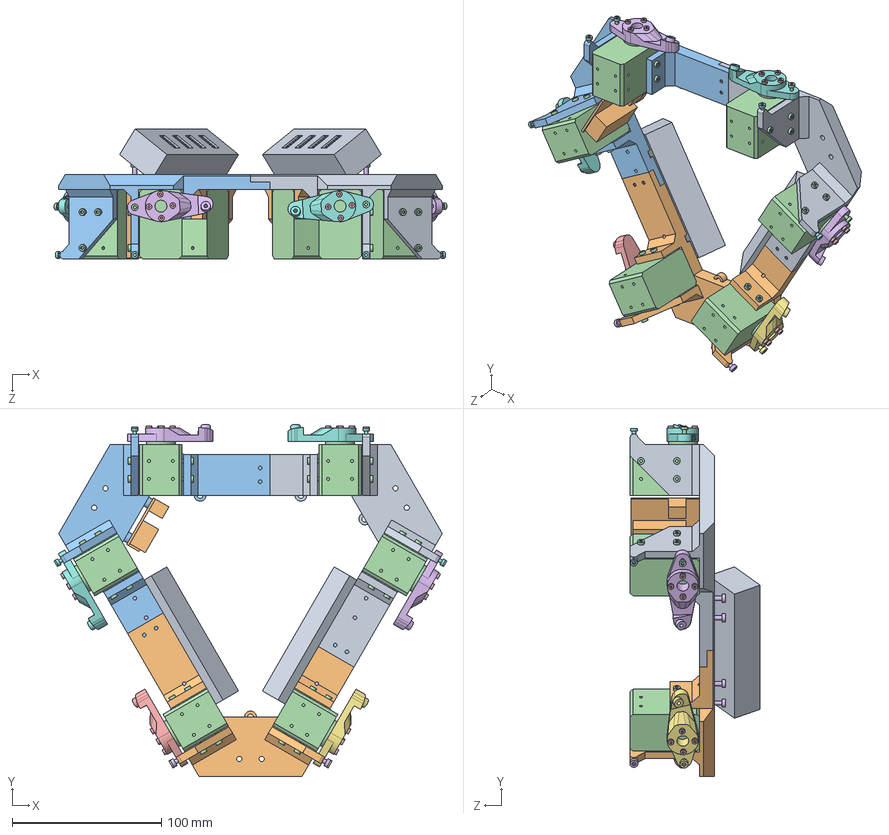
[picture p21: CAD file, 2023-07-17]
CAD/assemblies/stewart bottom.SLDASM
263.2 x 236.1 x 87.3 mm
stewart bottom 1
stewart bottom 2
stewart bottom 3
XL430-W250-T x 6
stewart horn left M3
stewart horn left M2.5 x 2
stewart horn right M3
stewart horn right M2.5 x 2
Anker USB-c hub (4 ports) x 2
dynamixel control
M3x6mm plastic x 6
M2.5x8mm plastic x 46
M2x12mm socket x 24
M3x12mm plastic x 10
M3x8mm plastic x 4
M2.5x12mm plastic x 4

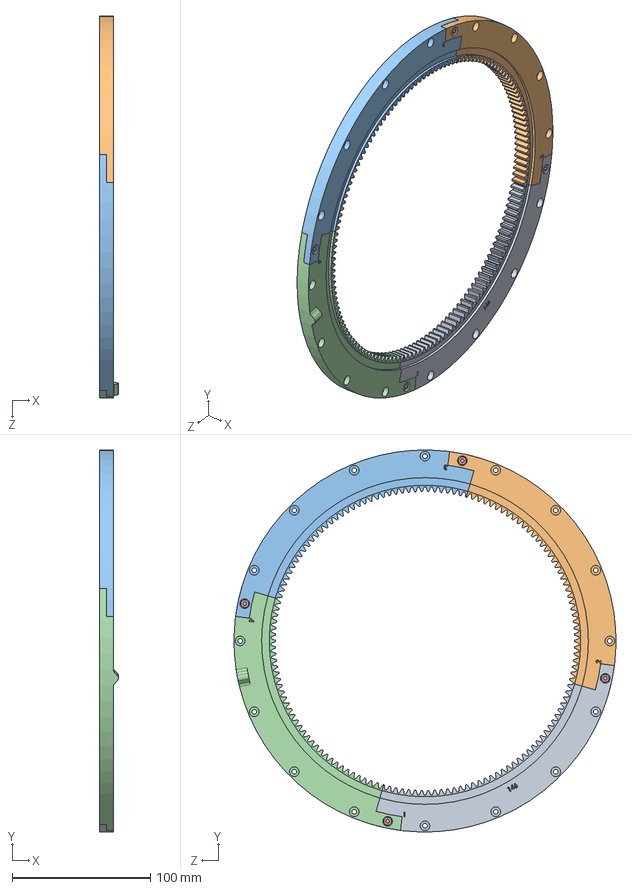
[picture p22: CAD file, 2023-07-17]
CAD/assemblies/base gear.SLDASM
13.7 x 275.9 x 275.9 mm
base gear 1
base gear 2
base gear 3
base gear 4
M3x6mm plastic x 4

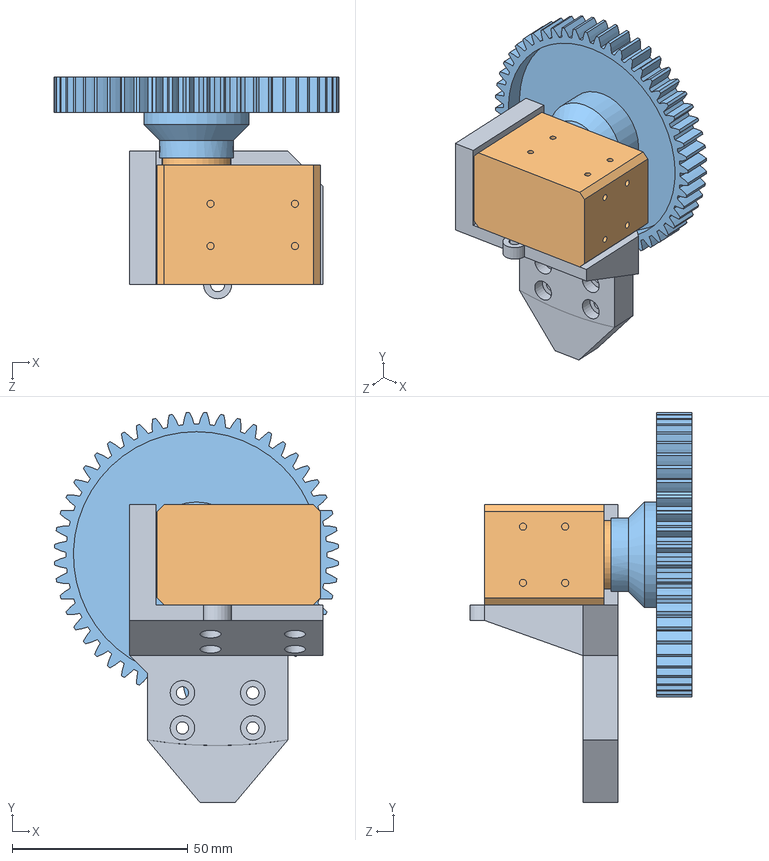
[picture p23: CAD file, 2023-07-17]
CAD/assemblies/gear servo bracket.SLDASM
80.9 x 110.9 x 63.0 mm
gear servo bracket
XL430-W250-T
torso bottom gear
M2.5x8mm plastic x 6
M2x12mm socket x 4

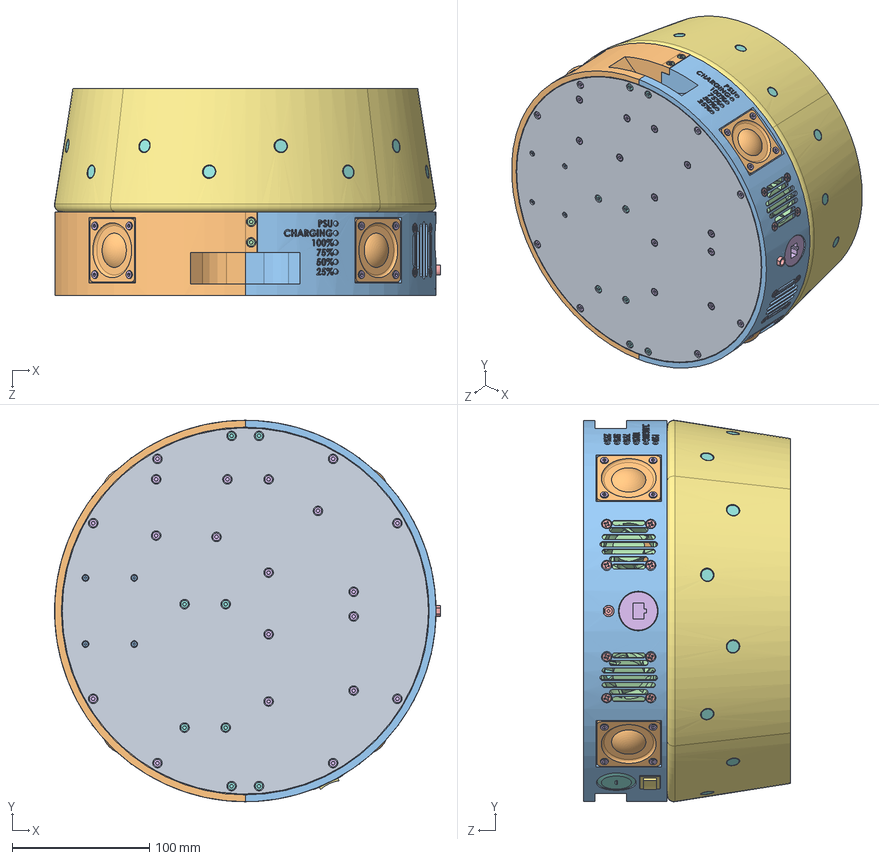
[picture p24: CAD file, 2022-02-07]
CAD/assemblies/base.SLDASM
281.5 x 278.3 x 151.0 mm
base disk
Adafruit MAX9744 x 2
Battery charger RRC-PMM240
battery holder
Battery RRC2054-2
ground loop noise isolator x 2
psu control
buck boost x 2
732-12936-ND x 4
732-12918-ND x 4
M2x5mm socket x 4
M2 nut x 4
36-24337-ND x 12
M3x5mm socket x 12
M3 nut x 12
M3x5mm plastic x 72
36-24342-ND x 4
base audio 1
base audio 2
Noctua NF-A4X20 x 2
SC2073-ND
RJ45 connector
switch
Micro USB B (Adafruit 4217)
Micro USB B nut (Adafruit 4217)
Dayton Audio DMA45-8 x 4
LED 5mm x 6
M3x12mm plastic x 12
fan screw x 8
M3x8mm plastic x 28
base mic x 4
8SoundsUSB Mic x 16
16SoundsUSB

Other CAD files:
CAD/3d printed parts/torso bottom internal xavier.SLDPRT
CAD/DXF/base disk.DXF
CAD/electronics/LED level.SLDPRT
CAD/hardware/stewart rod.SLDPRT
CAD/3d printed parts/USB hub stand.SLDPRT
CAD/3d printed parts/base audio back left.SLDPRT
CAD/3d printed parts/base audio back right.SLDPRT
CAD/3d printed parts/base audio front left.SLDPRT
CAD/3d printed parts/base audio front right.SLDPRT
CAD/3d printed parts/base gear 1.SLDPRT
CAD/3d printed parts/base gear 2.SLDPRT
CAD/3d printed parts/base gear 3.SLDPRT
CAD/3d printed parts/base gear 4.SLDPRT
CAD/3d printed parts/base gear.SLDPRT
CAD/3d printed parts/base mic.SLDPRT
CAD/3d printed parts/battery holder.SLDPRT
CAD/3d printed parts/gear servo bracket.SLDPRT
CAD/3d printed parts/head cable protector.SLDPRT
CAD/3d printed parts/head.SLDPRT
CAD/3d printed parts/limit switch bracket.SLDPRT
CAD/3d printed parts/stewart bottom 1.SLDPRT
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

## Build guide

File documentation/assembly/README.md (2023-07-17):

# Assembly

## Required Tools

- Screwdrivers
- Pliers
- Epoxy Glue
- Super Glue
- Tie Wraps
- Soldering Iron
- Solder
- Heat Gun
- Threadlocker (blue)
- JST XH Crimp Tool
- RJ12 Crimp Tool
- Micro USB Cable
- 12V Power Supply

## Assembly Instructions

0. [Orders/Print/Laser Cutting](00_ORDER_PRINT_LASER_CUTTING.md)
1. [Computer Configuration](01_COMPUTER_CONFIGURATION.md)
2. [PCB Assembly](02_PCB_ASSEMBLY.md)
3. [Dynamixel Configuration](03_DYNAMIXEL_CONFIGURATION.md)
4. [Cable Assembly](04_CABLE_ASSEMBLY.md)
5. [Base Disk Assembly](05_BASE_DISK_ASSEMBLY.md)
6. [Audio Base Assembly](06_AUDIO_BASE_ASSEMBLY.md)
7. [Mic Base Assembly](07_MIC_BASE_ASSEMBLY.md)
8. [Torso Bottom Assembly](08_TORSO_BOTTOM_ASSEMBLY.md)
9. [Stewart Platform Assembly](09_STEWART_PLATFORM_ASSEMBLY.md)
10. [Head Assembly](10_HEAD_ASSEMBLY.md)
11. [Robot Assembly](11_ROBOT_ASSEMBLY.md)
12. [MCU Configuration](12_MCU_CONFIGURATION.md)
13. [Calibration](13_CALIBRATION.md)

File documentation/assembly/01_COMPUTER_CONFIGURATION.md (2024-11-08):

# Computer Configuration

## Onboard Computer - Jetson AGX Xavier

### A. Install the Auto Power On Jumper

| Part | Quantity | Image |
| --- | --- | --- |
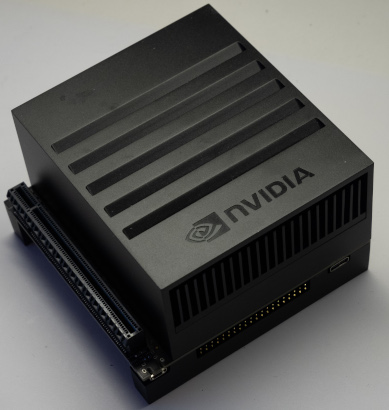
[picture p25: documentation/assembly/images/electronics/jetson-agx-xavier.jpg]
Nvidia Jetson AGX Xavier
| `Nvidia Jetson AGX Xavier` | 1 |  |
| `Jumper` | 1 | |

#### Steps

1. Install the jumper as shown in the following picture.

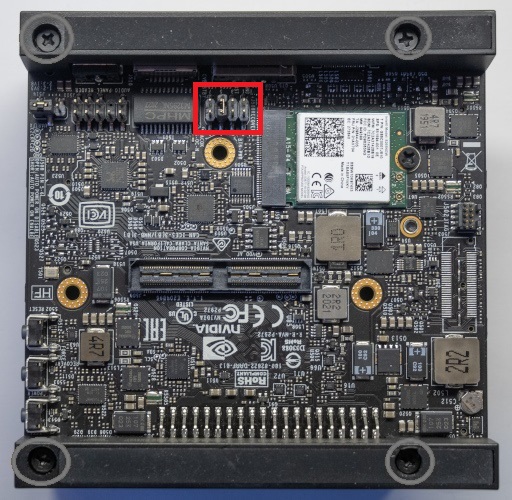
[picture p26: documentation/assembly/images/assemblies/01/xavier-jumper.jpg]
Nvidia Jetson AGX Xavier Jumper


### B. Install the SSD

#### Required Parts

| Part | Quantity | Image |
| --- | --- | --- |
| `Nvidia Jetson AGX Xavier` | 1 | Nvidia Jetson AGX Xavier |
| `SSD` | 1 | SSD |

#### Steps

1. Remove the following screws.

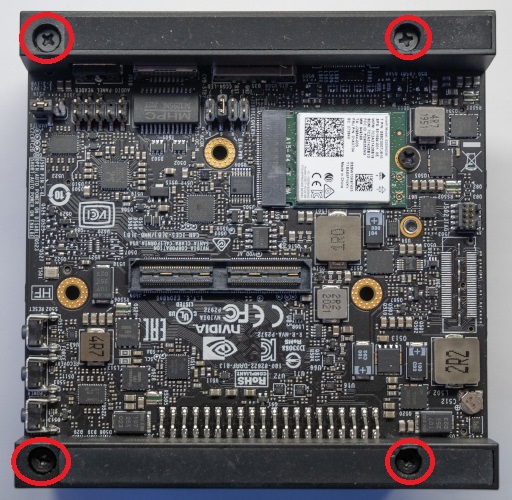
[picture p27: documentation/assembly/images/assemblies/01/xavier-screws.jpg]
Nvidia Jetson AGX Xavier Screws


2. Remove the bottom PCB.
3. Install the SSD, as shown in the following picture.

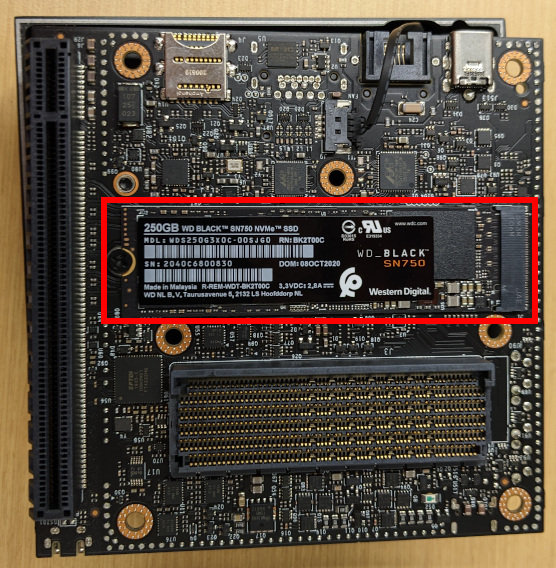
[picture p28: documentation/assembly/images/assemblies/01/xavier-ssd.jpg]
Nvidia Jetson AGX Xavier SSD


### C. Remove dV/dt protection feature

#### Required Parts

| Part | Quantity | Image |
| --- | --- | --- |
| `Nvidia Jetson AGX Xavier` | 1 | Nvidia Jetson AGX Xavier |

#### Steps

1. Remove R135 (see [P2822_B03_PCB_assembly_drawing.pdf](http://developer.nvidia.com/embedded/dlc/jetson-xavier-developer-kit-carrier-board-design-files-b03)).
2. Replace the bottom PCB.
1. Install the following screws.

Nvidia Jetson AGX Xavier Screws

### D. Install the WiFi Card

#### Required Parts

| Part | Quantity | Image |
| --- | --- | --- |
| `Nvidia Jetson AGX Xavier` | 1 | Nvidia Jetson AGX Xavier |
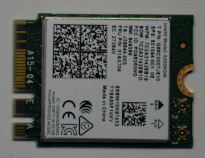
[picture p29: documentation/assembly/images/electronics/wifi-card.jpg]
WiFi Card
| `WiFi Card` | 1 |  |

#### Steps

1. Install the `WiFi card` into the `Nvidia Jetson AGX Xavier`.

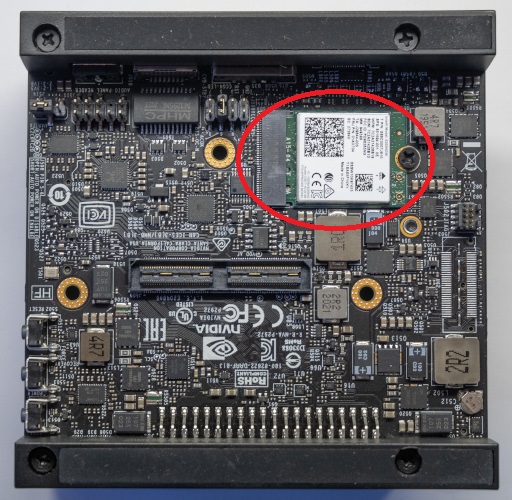
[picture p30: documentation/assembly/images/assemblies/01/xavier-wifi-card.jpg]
WiFi Card


## Onboard Computer - Jetson AGX Orin

### A. Install the SSD

#### Required Parts

| Part | Quantity | Image |
| --- | --- | --- |
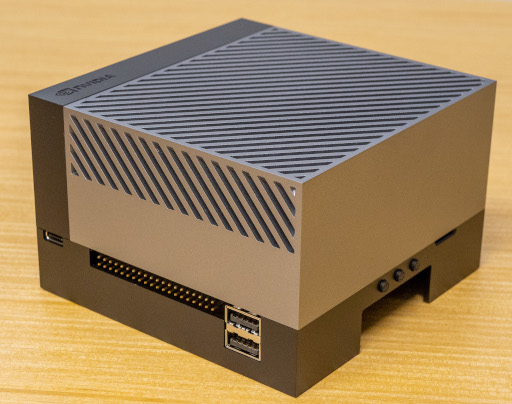
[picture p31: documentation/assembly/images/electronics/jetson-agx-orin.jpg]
Nvidia Jetson AGX Orin
| `Nvidia Jetson AGX Orin` | 1 |  |
| `SSD` | 1 | SSD |

#### Steps

1. Install the SSD, as shown in the following picture.

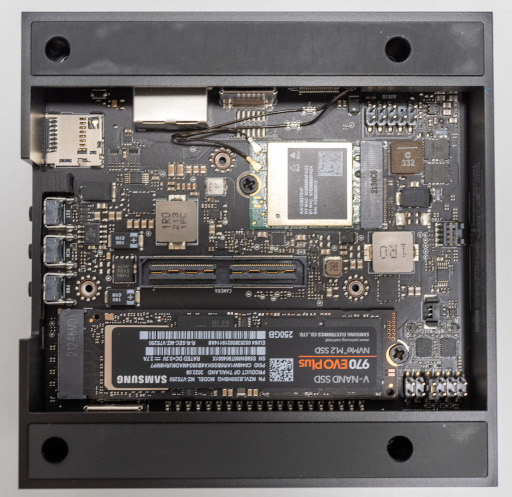
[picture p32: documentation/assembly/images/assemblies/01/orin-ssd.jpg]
Nvidia Jetson AGX Orin SSD


## Onboard Computer - Common Software Setup

### A. Install JetPack 5.1.1

1. Install JetPack 5.1.1 onto the computer SSD using the [instructions from Nvidia](https://developer.nvidia.com/embedded/jetpack)

### B. Connect the screen

#### Required Parts

| Part | Quantity | Image |
| --- | --- | --- |
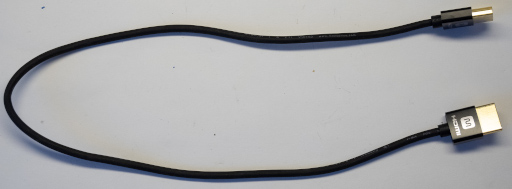
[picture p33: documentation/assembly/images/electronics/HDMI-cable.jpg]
HDMI Cable
| `HDMI Cable` | 1 |  |
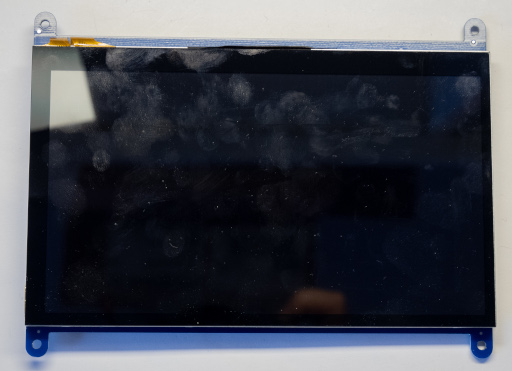
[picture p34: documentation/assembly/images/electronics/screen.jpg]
Touchscreen
| `Touchscreen` | 1 |  |

#### Steps

1. Connect the screen to the Jetson using the HDMI cable.
2. Turn on the `touchscreen` as shown in the following picture.

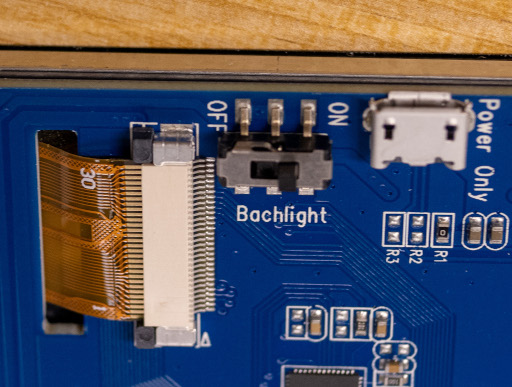
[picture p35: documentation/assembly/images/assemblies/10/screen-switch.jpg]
Touchscreen Switch


### C. Rotate the display
1. Open "Settings"
2. Navigate to the "Display" tab
3. Set the orientation to 'Portrait Left" a shown below

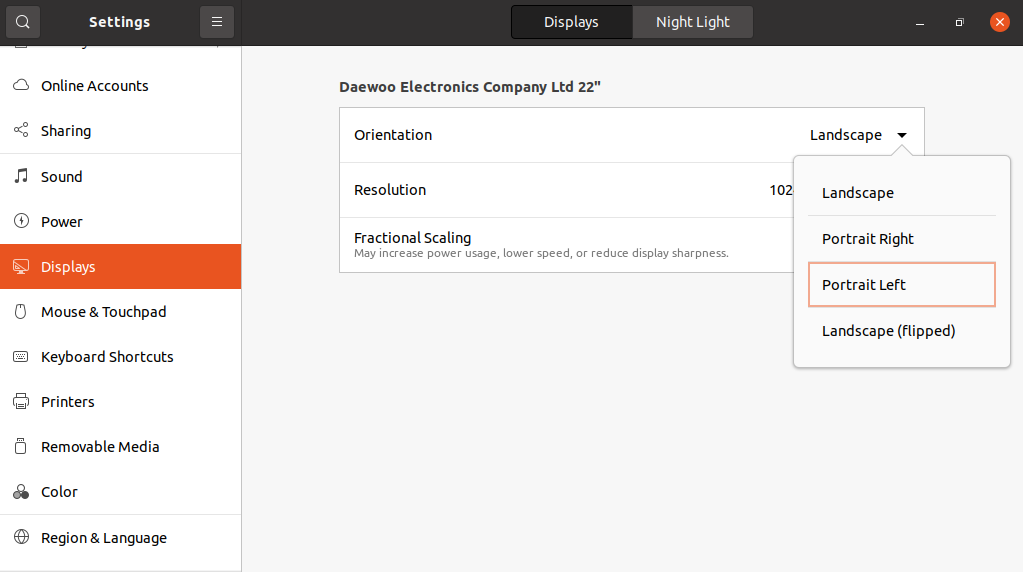
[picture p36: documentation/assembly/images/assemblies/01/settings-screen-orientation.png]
Settings Screen Orientation


4. Select "Keep changes" when prompted

### D. Run the setup script

1. Execute the following bash command on the robot.

```bash
wget -q -O - https://raw.githubusercontent.com/introlab/t-top/main/tools/setup_scripts/jetson_configuration.sh | bash
```

#### Alternate way: manual setup

### D. Update the robot
Execute the following bash commands on the robot.

```bash
sudo apt update
sudo apt upgrade -y
sudo apt autoremove -y
```

### E. Clone the repository
Execute the following bash commands on the robot to clone the T-Top repository.

```bash
mkdir -p ~/t-top_ws/src
cd ~/t-top_ws/src

git clone --recurse-submodules https://github.com/introlab/t-top.git
```

### F. Configure the Jetson power mode
For the Jetson AGX Xavier, execute the following bash command on the robot.

```bash
sudo nvpmodel -m 0
```

For the Jetson AGX Orin, execute the following bash commands on the robot.

```bash
sudo cp /etc/nvpmodel.conf /etc/nvpmodel/nvpmodel.conf.backup
sudo cp ~/t-top_ws/src/t-top/tools/setup_scripts/files/jetson_orin_nvpmodel.conf /etc/nvpmodel.conf

sudo nvpmodel -m 1 &> /dev/null
sudo nvpmodel -m 0
```

### G. System configuration
1. Disable the sudo password requirement for `shutdown` and `nvpmodel` by executing the following bash command on the robot.

```bash
sudo cp ~/t-top_ws/src/t-top/tools/setup_scripts/files/sudoers_ttop /etc/sudoers.d/ttop
```

2. Copy [99-teensy.rules](../../tools/udev_rules/99-teensy.rules) in `/etc/udev/rules.d/`.

```bash
sudo cp ~/t-top_ws/src/t-top/tools/udev_rules/99-teensy.rules /etc/udev/rules.d/
```

3. Copy [99-camera-2d-wide.rules](../../tools/udev_rules/99-camera-2d-wide.rules) in `/etc/udev/rules.d/`.

```bash
sudo cp ~/t-top_ws/src/t-top/tools/udev_rules/99-camera-2d-wide.rules /etc/udev/rules.d/
```

4. Add the user to the `dialout` group by executing the following bash command on the robot.

```bash
sudo usermod -a -G dialout $USER
```

5. Setup autologin in the settings menu.

6. Disable automatic sleep and screen lock by executing the following bash commands on the robot.

```bash
gsettings set org.gnome.desktop.screensaver ubuntu-lock-on-suspend 'false'
gsettings set org.gnome.desktop.screensaver lock-delay 0
gsettings set org.gnome.desktop.session idle-delay 0
```

8. Add `Option "CalibrationMatrix" "0 1 0 -1 0 1 0 0 1"` before `EndSection` in the following section of `/usr/share/X11/xorg.conf.d/40-libinput.conf`.

```
Section "InputClass"
        Identifier "libinput touchscreen catchall"
        MatchIsTouchscreen "on"
        MatchDevicePath "/dev/input/event*"
        Driver "libinput"
EndSection
```

### H. Install NPM
1. Execute the following bash commands.

```bash
sudo apt install -y curl software-properties-common
curl -sL https://deb.nodesource.com/setup_14.x | sudo -E bash -
sudo apt install -y nodejs
```

### I. Install Tools
1. Execute the following bash commands.

```bash
sudo apt install -y htop python3-pip perl
sudo -H pip3 install -U jetson-stats

# Update CMake
wget -O - https://apt.kitware.com/keys/kitware-archive-latest.asc 2>/dev/null | gpg --dearmor - | sudo tee /etc/apt/trusted.gpg.d/kitware.gpg >/dev/null
sudo apt-add-repository "deb https://apt.kitware.com/ubuntu/ $(lsb_release -cs) main"
sudo apt update
sudo apt install -y cmake
```

### J. Install Librealsense 2
1. Execute the following bash commands.

```bash
mkdir ~/deps
cd ~/deps

git clone https://github.com/jetsonhacks/buildLibrealsense2Xavier.git
cd buildLibrealsense2Xavier
```

2. Change the version to `v2.50.0` in `installLibrealsense.sh`.
3. Add the folowing arguments to the `cmake` command in `installLibrealsense.sh`.

```bash
-DCMAKE_CXX_FLAGS="-march=native -ffast-math" -DCMAKE_C_FLAGS="-march=native -ffast-math"
```

4. Execute the following bash commands.

```bash
# Cannot be installed to build librealsense
sudo apt autoremove -y libapriltag-dev
./installLibrealsense.sh
sudo apt install -y libapriltag-dev
```

### K. Install ROS
1. Execute the following bash commands.

```bash
sudo sh -c 'echo "deb http://packages.ros.org/ros/ubuntu $(lsb_release -sc) main" > /etc/apt/sources.list.d/ros-latest.list'
curl -s https://raw.githubusercontent.com/ros/rosdistro/master/ros.asc | sudo apt-key add -
sudo apt update

sudo apt install -y \
    python3-rosdep \
    python3-rosinstall-generator \
    python3-vcstool \
    build-essential \
    libboost-all-dev \
    libpoco-dev \
    python3-empy \
    libtinyxml-dev \
    libtinyxml2-dev \
    qt5-default \
    sip-dev \
    python3-sip \
    python3-sip-dbg \
    python3-sip-dev \
    python3-pyqt5 \
    python3-nose \
    python3-twisted \
    python3-serial \
    python3-autobahn \
    python3-tornado \
    python3-bson \
    python3-qt-binding \
    libcurl4-gnutls-dev \
    libgtest-dev \
    liblz4-dev \
    libfltk1.1-dev \
    liburdfdom-headers-dev \
    liburdfdom-dev \
    liburdfdom-tools \
    libgpgme-dev \
    libyaml-cpp-dev \
    libpcl-dev \
    libgtk-3-dev \
    libassimp-dev \
    libogre-1.9-dev \
    libconfig-dev \
    liblog4cplus-dev \
    alsa-utils \
    liblog4cpp5-dev \
    liblog4cxx-dev \
    libbz2-dev \
    libbullet-dev \
    libsdl1.2-dev \
    libsdl-image1.2-dev \
    libapriltag-dev \
    libdc1394-22-dev

# Install system dependencies
cd ~/deps
git clone https://github.com/ros/console_bridge.git
cd console_bridge
mkdir build
cd build
cmake .. -DCMAKE_BUILD_TYPE=Release -DCMAKE_CXX_FLAGS="-march=native -ffast-math" -DCMAKE_C_FLAGS="-march=native -ffast-math"
cmake --build .
sudo cmake --install .

cd ~/deps
git clone https://github.com/ethz-asl/libnabo.git
cd libnabo
mkdir build
cd build
cmake .. -DCMAKE_BUILD_TYPE=Release -DCMAKE_CXX_FLAGS="-march=native -ffast-math" -DCMAKE_C_FLAGS="-march=native -ffast-math"
cmake --build .
sudo cmake --install .

cd ~/deps
git clone https://github.com/ethz-asl/libpointmatcher.git
cd libpointmatcher
mkdir build
cd build
cmake .. -DCMAKE_BUILD_TYPE=Release -DCMAKE_CXX_FLAGS="-march=native -ffast-math" -DCMAKE_C_FLAGS="-march=native -ffast-math"
cmake --build .
sudo cmake --install .

cd ~/deps
git clone -b 0.21.1-noetic https://github.com/introlab/rtabmap.git
cd rtabmap/build
cmake .. -DCMAKE_BUILD_TYPE=Release -DCMAKE_CXX_FLAGS="-march=native -ffast-math" -DCMAKE_C_FLAGS="-march=native -ffast-math"
cmake --build . -j4
sudo cmake --install .

# Install ROS
sudo rosdep init
rosdep update

mkdir -p ~/ros_catkin_ws/src
cd ~/ros_catkin_ws

rosinstall_generator desktop_full --rosdistro noetic --deps --tar > noetic-desktop.rosinstall
vcs import --input noetic-desktop.rosinstall ./src
rosdep install --from-paths ./src --ignore-packages-from-source --rosdistro noetic -y

# Remove useless packages
rm -rf ~/ros_catkin_ws/src/gazebo_ros_pkgs/

# Add ROS packages
cd ~/ros_catkin_ws/src
git clone -b 1.0.1 https://github.com/GT-RAIL/rosauth.git
git clone -b noetic-devel https://github.com/ros-drivers/rosserial.git
git clone -b ros1 https://github.com/RobotWebTools/rosbridge_suite.git
git clone -b noetic https://github.com/ccny-ros-pkg/imu_tools.git
git clone --recursive https://github.com/orocos/orocos_kinematics_dynamics.git

git clone -b 0.21.1-noetic https://github.com/introlab/rtabmap_ros.git
git clone -b noetic-devel https://github.com/ros-planning/navigation.git

git clone -b kinetic-devel https://github.com/pal-robotics/ddynamic_reconfigure.git
git clone -b 2.3.2 https://github.com/IntelRealSense/realsense-ros.git
git clone https://github.com/OTL/cv_camera.git
git clone -b 0.6.4-noetic https://github.com/introlab/find-object.git

# Replace not complete packages
rm -rf geometry2 navigation_msgs vision_opencv image_common perception_pcl pcl_msgs image_transport_plugins

git clone -b noetic-devel https://github.com/ros/geometry2.git
git clone -b ros1 https://github.com/ros-planning/navigation_msgs.git
git clone -b noetic https://github.com/ros-perception/vision_opencv.git
git clone -b noetic-devel https://github.com/ros-perception/image_common.git

git clone -b 1.7.1 https://github.com/ros-perception/perception_pcl.git
git clone -b noetic-devel https://github.com/ros-perception/pcl_msgs.git
git clone -b noetic-devel https://github.com/ros-perception/image_transport_plugins.git

cd ~/ros_catkin_ws
rosdep install --from-paths ./src/image_transport_plugins --ignore-packages-from-source --rosdistro noetic -y
# Can not be installed for the build, as CMake will pick it instead of the system 3.8
sudo apt autoremove -y python3.9

catkin config --init --install --space-suffix _isolated --cmake-args -DCMAKE_BUILD_TYPE=Release -DCMAKE_CXX_FLAGS="-march=native -ffast-math" -DCMAKE_C_FLAGS="-march=native -ffast-math" -DPYTHON_EXECUTABLE=/usr/bin/python3 -DCATKIN_ENABLE_TESTING=0 -Wno-dev
catkin build

# Add ROS setup to .bashrc
echo "source ~/ros_catkin_ws/install_isolated/setup.bash" >> ~/.bashrc
source ~/.bashrc
```

### L. Install System Dependencies

1. Execute the following bash commands.

```bash
sudo apt install -y \
    libasound2-dev \
    libpulse-dev \
    libconfig-dev \
    alsa-utils \
    gfortran \
    libgfortran-*-dev \
    texinfo \
    libfftw3-dev \
    libsqlite3-dev \
    portaudio19-dev \
    python3-all-dev \
    libgecode-dev \
    qt5-default \
    v4l-utils \
    libopenblas-dev \
    libpython3-dev \
    ffmpeg \
    chromium-browser \
    libqt5websockets5-dev \
    libqt5charts5-dev \
    libgstreamer1.0-dev \
    libgstreamer-plugins-base1.0-dev \
    libgstreamer-plugins-good1.0-dev \
    libgstreamer-plugins-bad1.0-dev \
    gstreamer1.0-plugins-base \
    gstreamer1.0-plugins-good \
    gstreamer1.0-plugins-bad \
    gstreamer1.0-plugins-ugly \
    gstreamer1.0-libav \
    gstreamer1.0-tools \
    libspdlog-dev \
    scons

# Install onnxruntime
cd ~/deps
git clone https://github.com/microsoft/onnxruntime.git -b v1.14.1 --recurse-submodules
cd onnxruntime
./build.sh --config Release --update --build --parallel --build_wheel --build_shared_lib --use_tensorrt --cuda_home /usr/local/cuda --cudnn_home /usr/lib/aarch64-linux-gnu --tensorrt_home /usr/lib/aarch64-linux-gnu
cd build/Linux/Release
sudo make install

# Install ComputeLibrary
cd ~/deps
git clone --depth 1 -b v22.11 https://github.com/ARM-software/ComputeLibrary.git
cd ComputeLibrary
scons Werror=1 -j8 debug=0 neon=1 opencl=0 os=linux arch=armv8a build=native
mv build lib

# Install onDNN
cd ~/deps
git clone --depth 1 -b v3.2.1 https://github.com/oneapi-src/oneDNN.git
cd oneDNN
mkdir build
cd build
export ACL_ROOT_DIR=~/deps/ComputeLibrary
cmake .. -DCMAKE_BUILD_TYPE=Release -DCMAKE_CXX_FLAGS="-march=native -ffast-math" -DCMAKE_C_FLAGS="-march=native -ffast-math -DDNNL_AARCH64_USE_ACL=ON"
cmake --build . -j4
sudo cmake --install .
```

### M. Install Python Dependencies

1. Execute the following bash commands.

```bash
# Install general dependencies
sudo apt install -y \
    'libprotobuf*' \
    protobuf-compiler \
    ninja-build \
    python3-numpy \
    python3-scipy \
    python3-numba \
    python3-matplotlib \
    python3-sklearn \
    python3-tqdm \
    python3-audioread \
    python3-requests \
    python3-sphinx

sudo -H pip3 install 'cython>=0.29.22,<0.30.0'
sudo -H pip3 install -r ~/t-top_ws/src/t-top/tools/setup_scripts/files/requirements.txt

#Install CTranslate2
cd ~/deps
git clone --depth 1 -b v3.20.0 https://github.com/OpenNMT/CTranslate2.git --recurse-submodule
cd CTranslate2
mkdir build
cd build
cmake .. -DCMAKE_BUILD_TYPE=Release -DCMAKE_CXX_FLAGS="-march=native -ffast-math" -DCMAKE_C_FLAGS="-march=native -ffast-math" -DWITH_MKL=OFF -DWITH_CUDA=ON -DWITH_CUDNN=ON -DWITH_OPENBLAS=ON -DWITH_DNNL=ON -DWITH_RUY=ON
cmake --build . -j4
sudo cmake --install .
sudo ldconfig
cd ../python
sudo -H pip3 install -r install_requirements.txt
python3 setup.py bdist_wheel
sudo -H pip3 install dist/*.whl --no-deps --force-reinstall

# Install PyTorch for Jetson
cd ~/deps
wget https://developer.download.nvidia.com/compute/redist/jp/v50/pytorch/torch-1.12.0a0+2c916ef.nv22.3-cp38-cp38-linux_aarch64.whl
sudo -H pip3 install torch-1.12.0a0+2c916ef.nv22.3-cp38-cp38-linux_aarch64.whl

cd ~/deps
git clone --depth 1 -b v0.13.0 https://github.com/pytorch/vision.git
cd vision
mkdir -p build
cd build
cmake .. -DCMAKE_BUILD_TYPE=Release -DCMAKE_CXX_FLAGS="-march=native -ffast-math" -DCMAKE_C_FLAGS="-march=native -ffast-math" -DCMAKE_PREFIX_PATH=`python3 -c 'import torch;print(torch.utils.cmake_prefix_path)'` -DWITH_CUDA=ON
cmake --build . -j4
sudo cmake --install .
cd ~/deps/vision
sudo -H python3 setup.py install

cd ~/deps
git clone --depth 1 -b v0.12.0 https://github.com/pytorch/audio.git --recurse-submodule
cd audio
sudo bash -c 'echo "export PATH=/usr/local/cuda-11.4/bin:\$PATH" >> /root/.bashrc'
sudo bash -c 'sudo echo "export LD_LIBRARY_PATH=/usr/local/cuda-11.4/lib64:\$LD_LIBRARY_PATH" >> /root/.bashrc'
sudo -H pip3 install -r requirements.txt
sudo -H bash -c 'TORCH_CUDA_ARCH_LIST="7.2;8.7" CUDACXX=/usr/local/cuda/bin/nvcc python3 setup.py install'

cd ~/deps
git clone https://github.com/NVIDIA-AI-IOT/torch2trt
cd torch2trt
sudo -H python3 setup.py install --plugins
```

### N. Install the T-Top hardware daemon and system tray
1. Build and install the daemon:
```bash
cd ~/t-top_ws/src/t-top/system/daemon
mkdir build
cd build
cmake .. -DCMAKE_BUILD_TYPE=Release -DCMAKE_CXX_FLAGS="-march=native -ffast-math" -DCMAKE_C_FLAGS="-march=native -ffast-math"
cmake --build .
sudo cmake --install .
```
2. Build and install the system tray:
```bash
cd ~/t-top_ws/src/t-top/system/system_tray
mkdir build
cd build
cmake .. -DCMAKE_BUILD_TYPE=Release -DCMAKE_CXX_FLAGS="-march=native -ffast-math" -DCMAKE_C_FLAGS="-march=native -ffast-math"
cmake --build .
sudo cmake --install .
```
3. Enable the deamon service:
```bash
sudo systemctl enable ttop_hardware_daemon.service
sudo systemctl start ttop_hardware_daemon.service
```

### O. Build the Repository

1. Execute the following bash commands.

```bash
cd ~/t-top_ws

# Default development profile, using Debug
catkin config --init --cmake-args -DCMAKE_BUILD_TYPE=Debug -DCMAKE_CXX_FLAGS="-march=native -ffast-math" -DCMAKE_C_FLAGS="-march=native -ffast-math" -DPYTHON_EXECUTABLE=/usr/bin/python3 -DCMAKE_WARN_DEPRECATED=OFF -DCMAKE_EXPORT_COMPILE_COMMANDS=ON
# Release profile, build with 'catkin build --profile release'
catkin config --profile release --init --space-suffix _release --cmake-args -DCMAKE_BUILD_TYPE=Release -DCMAKE_CXX_FLAGS="-march=native -ffast-math" -DCMAKE_C_FLAGS="-march=native -ffast-math" -DPYTHON_EXECUTABLE=/usr/bin/python3 -DCMAKE_WARN_DEPRECATED=OFF -DCMAKE_EXPORT_COMPILE_COMMANDS=ON

catkin build
```

## Development Computer (Ubuntu 20.04)

### A. OpenCR Dev Rule

1. Copy [99-opencr-custom.rules](../../tools/udev_rules/99-opencr-custom.rules) in `/etc/udev/rules.d/`.
2. Copy [99-teensy.rules](../../tools/udev_rules/99-teensy.rules) in `/etc/udev/rules.d/`.
2. Copy [99-camera-2d-wide.rules](../../tools/udev_rules/99-camera-2d-wide.rules) in `/etc/udev/rules.d/`.
3. Add the user to the `dialout` group.

```bash
sudo usermod -a -G dialout $USER
```

### B. Install NPM

1. Execute the following bash commands.

```bash
sudo apt install -y curl software-properties-common
curl -sL https://deb.nodesource.com/setup_14.x | sudo -E bash -
sudo apt install -y nodejs
```

### C. Install ROS

1. Execute the following bash commands.

```bash
sudo sh -c 'echo "deb http://packages.ros.org/ros/ubuntu $(lsb_release -sc) main" > /etc/apt/sources.list.d/ros-latest.list'
curl -s https://raw.githubusercontent.com/ros/rosdistro/master/ros.asc | sudo apt-key add -
sudo apt update

sudo apt install -y ros-noetic-desktop-full
echo "source /opt/ros/noetic/setup.bash" >> ~/.bashrc
source ~/.bashrc
sudo rosdep init
rosdep update
sudo apt install -y \
    python3-rosinstall \
    python3-rosinstall-generator \
    python3-wstool \
    build-essential \
    ros-noetic-rosserial-python \
    ros-noetic-rosbridge-suite \
    ros-noetic-ddynamic-reconfigure \
    ros-noetic-imu-filter-madgwick \
    ros-noetic-cv-bridge \
    ros-noetic-rtabmap-ros \
    ros-noetic-cv-camera
```

### D. Install System Dependencies

1. Execute the following bash commands.

```bash
sudo apt install -y libasound2-dev \
    libpulse-dev \
    libconfig-dev \
    alsa-utils \
    gfortran \
    'libgfortran-*-dev' \
    texinfo \
    libfftw3-dev \
    libsqlite3-dev \
    portaudio19-dev \
    python3-all-dev \
    libgecode-dev \
    qt5-default \
    v4l-utils
```

### E. Install Python Dependencies

1. Execute the following bash commands.

```bash
sudo apt install -y 'libprotobuf*' protobuf-compiler ninja-build python3-pip python3-sklearn
sudo -H pip3 install numpy scipy matplotlib torch==1.11.0 torchvision==0.12.0 torchaudio==0.11.0 google-cloud-texttospeech google-cloud-speech libconf tqdm pyside2 sounddevice librosa requests ipinfo
sudo -H pip3 install 'git+https://github.com/cocodataset/cocoapi.git#subdirectory=PythonAPI'
```

### F. Install CUDA Tools (Optional)

1. Install [TensorRT](https://docs.nvidia.com/deeplearning/tensorrt/install-guide/index.html).
2. Install torch2trt.

```bash
cd ~/deps
git clone https://github.com/NVIDIA-AI-IOT/torch2trt
cd torch2trt
sudo python3 setup.py install --plugins
```

### G. Clone the Repository

1. Execute the following bash commands.

```bash
mkdir ~/t-top_ws
cd ~/t-top_ws
mkdir src
catkin_make

cd src
git clone --recurse-submodules git@github.com:introlab/t-top.git
```

### H. Install the RealSense Packages
1. Install [Librealsense](https://github.com/IntelRealSense/librealsense/blob/v2.39.0/doc/installation.md) (use the tag
   v2.50.0).
2. Install [ROS node](https://github.com/IntelRealSense/realsense-ros#step-2-install-intel-realsense-ros-from-sources)
   in `~/t-top_ws/src` (use the tag 2.3.2)

## All computer

### A. Setup Google Cloud

1. Create
   a [service account JSON keyfile](https://cloud.google.com/iam/docs/creating-managing-service-accounts#creating) for
   Google Cloud Text-to-Speech and Google Cloud Speech-to-Text.
2. Add the following line to `~/.bashrc`

```bash
export GOOGLE_APPLICATION_CREDENTIALS="[Path to the service account JSON keyfile]"
```

### B. Setup OpenWeatherMap

1. Create an [OpenWeatherMap API Key](https://home.openweathermap.org/users/sign_up).
2. Add the following line to `~/.bashrc`

```bash
export OPEN_WEATHER_MAP_API_KEY="[The key]"
```

### C. Setup a Different ROS2 Domain on Each Robot

1. Add the following line to `~/.bashrc`

```bash
# Avoid default=0 and make sure each robot has a different domain ID.
export ROS_DOMAIN_ID=[1...101]
```

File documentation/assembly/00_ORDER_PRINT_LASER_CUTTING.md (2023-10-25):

# Orders

In order to assemble the robot, you need to buy the following Items.

## Bill of Materials Excluding Custom PCBs.

The robot can use a Jetson AGX Xavier or a Jetson AGX Orin.
The Xavier and the Orin columns indicate whether the part is required with the Jetson AGX Xavier and the Jetson AGX Orin respectively.

### Digi-Key

| Part | Xavier | Orin | Quantity | Quantity per Package | Package Quantity | Link |
| --- | --- | ---- | --- | --- | --- | --- |
| Audio Amplifier - Adafruit MAX9744 | X | X | 2 | 1 | 2 | [Link](https://www.digikey.ca/en/products/detail/adafruit-industries-llc/1752/4990780) |
| Robot Power Connector - Female | X | X | 1 | 1 | 1 | [Link](https://www.digikey.ca/en/products/detail/switchcraft-inc/ST10U/4966994) |
| Robot Power Connector - Male | X | X | 1 | 1 | 1 | [Link](https://www.digikey.ca/en/products/detail/switchcraft-inc/S10KS12/3909315) |
| 19V Power Adapter | X | X | 1 | 1 | 1 | [Link](https://www.digikey.ca/en/products/detail/globtek-inc/TR9CZ9470CCPIMR6B/9837864) |
| Computer Power Connector - Male | X | X | 1 | 1 | 1 | [Link](https://www.digikey.ca/en/products/detail/172-4208/172-4208-ND/2439192) |
| Power Switch | X | X | 1 | 1 | 1 | [Link](https://www.digikey.ca/en/products/detail/e-switch/RA812C1121/3778076) |
| Micro USB Connector | X | X | 1 | 1 | 1 | [Link](https://www.digikey.ca/en/products/detail/adafruit-industries-llc/4217/10244658) |
| Ethernet Connector | X | X | 1 | 1 | 1 | [Link](https://www.digikey.ca/en/products/detail/harting/09454521561/8033369) |
| Jumper | X | | 1 | 1 | 1 | [Link](https://www.digikey.ca/en/products/detail/sullins-connector-solutions/QPC02SXGN-RC/2618262)  |
| WiFi Antenna | X | | 2 | 1 | 2 | [Link](https://www.digikey.ca/en/products/detail/molex/2042811200/8020428) |
| Intel RealSense D435i | X | X | 1 | 1 | 1 | [Link](https://www.digikey.ca/en/products/detail/intel-realsense/82635D435IDK5P/9926004) |
| Standoff - M2x10mm | X | X | 4 | 1 | 4 | [Link](https://www.digikey.ca/en/products/detail/wurth-electronics-inc/971100244/9488622) |
| Standoff - M2x15mm | X | X | 4 | 1 | 4 | [Link](https://www.digikey.ca/en/products/detail/w%C3%BCrth-elektronik/971150244/9488640) |
| Standoff - M3x10mm | X | X | 8 | 1 | 8 | [Link](https://www.digikey.ca/en/products/detail/keystone-electronics/24337/1532138) |
| Standoff - M3x25mm | X | X | 4 | 1 | 4 | [Link](https://www.digikey.ca/en/products/detail/keystone-electronics/24342/1532143) |
| Standoff - M3x10mm - Plastic | X | X | 4 | 1 | 4 | [Link](https://www.digikey.ca/en/products/detail/keystone-electronics/25501/1532180) |
| M3 Plastic Nuts | X | X | 4 | 1 | 4 | [Link](https://www.digikey.ca/en/products/detail/w%C3%BCrth-elektronik/709940300/9488341) |
| JST B2P-VH | X | X | 2 | 1 | 2 | [Link](https://www.digikey.ca/en/products/detail/te-connectivity-amp-connectors/1-1123723-2/686925) |
| JST VHR-2N | X | X | 2 | 1 | 2 | [Link](https://www.digikey.ca/en/products/detail/te-connectivity-amp-connectors/1744416-2/4730260)  |
| JST SVH-21T-1.1 | X | X | 4 | 1 | 4 | [Link](https://www.digikey.ca/en/products/detail/te-connectivity-amp-connectors/1744201-1/4021812)  |
| Push Button | X | X | 4 | 1 | 4 | [Link](https://www.digikey.ca/en/products/detail/e-switch/RP3502ABLK/280446) |
| Light Sensor | X | X | 4 | 1 | 4 | [Link](https://www.digikey.ca/en/products/detail/adafruit-industries-llc/2748/5775538) |

### McMaster-Carr

| Part | Xavier | Orin | Quantity | Quantity per Package | Package Quantity | Link |
| --- | --- | ---- | --- | --- | --- | --- |
| Plastic Screw - M2x5mm | X | X | 4 | 25 | 1 | [Link](https://www.mcmaster.com/96817A207/) |
| Plastic Screw - M2.5x5mm | X | X | 4 | 25 | 1 | [Link](https://www.mcmaster.com/96817A263/) |
| Plastic Screw - M2.5x8mm | X | X | 52 | 25 | 3 | [Link](https://www.mcmaster.com/96817A268/) |
| Plastic Screw - M2.5x12mm | X | X | 6 | 25 | 1 | [Link](https://www.mcmaster.com/96817A274/) |
| Plastic Screw - M3x5mm | X | X | 68 | 25 | 3 | [Link](https://www.mcmaster.com/96817A300/) |
| Plastic Screw - M3x6mm | X | X | 16 | 25 | 1 | [Link](https://www.mcmaster.com/96817A310/) |
| Plastic Screw - M3x8mm | X | X | 50 | 25 | 2 | [Link](https://www.mcmaster.com/96817A330/) |
| Plastic Screw - M3x12mm | X | X | 84 | 25 | 4 | [Link](https://www.mcmaster.com/96817A370/) |
| Plastic Screw - M5x10mm | X | X | 3 | 25 | 1 | [Link](https://www.mcmaster.com/96817A620/) |
| Socket Cap Screw - M2x5mm | X | X | 4 | 100 | 1 | [Link](https://www.mcmaster.com/91290A012/) |
| Socket Cap Screw - M2x12mm | X | X | 28 | 100 | 1 | [Link](https://www.mcmaster.com/91290A019/) |
| Socket Cap Screw - M3x5mm | X | X | 18 | 100 | 1 | [Link](https://www.mcmaster.com/91290A110/) |
| Socket Cap Screw - M3x10mm | X | X | 6 | 100 | 1 | [Link](https://www.mcmaster.com/91290A115/) |
| Socket Cap Screw - M3x55mm | X | | 4 | 1 | 4 | [Link](https://www.mcmaster.com/91290A573/) |
| Socket Cap Screw - M5x16mm | X | X | 6 | 100 | 1 | [Link](https://www.mcmaster.com/91290A232/) |
| Socket Cap Screw - M5x30mm | X | X | 3 | 10 | 1 | [Link](https://www.mcmaster.com/91290A194/) |
| M2 Nuts | X | X | 4 | 100 | 1 | [Link](https://www.mcmaster.com/90592A075/) |
| M3 Nuts | X | X | 10 | 100 | 1 | [Link](https://www.mcmaster.com/90592A085/) |
| M5 Washer | X | X | 18 | 100 | 1 | [Link](https://www.mcmaster.com/90965A160/) |
| Dowel Pin | X | X | 2 | 50 | 1 | [Link](https://www.mcmaster.com/97155A426/) |
| Small Spring | X | X | 4 | 5 | 1 | [Link](https://www.mcmaster.com/5108N032/)  |
| Big Spring | X | X | 2 | 5 | 1 | [Link](https://www.mcmaster.com/5108N209/)  |
| Diffuser Plastic Sheet | X | X | 1 | 1 | 1 | [Link](https://www.mcmaster.com/8657K311/)  |
| Cast Acrylic Sheet | X | X | 1 | 1 | 1 | [Link](https://www.mcmaster.com/8505K758/)  |

### Robotis

| Part | Xavier | Orin | Quantity | Quantity per Package | Package Quantity | Link |
| --- | --- | ---- | --- | --- | --- | --- |
| Dynamixel XL430-W250-T | X | X | 7 | 1 | 7 | [Link](https://www.robotis.us/dynamixel-xl430-w250-t/) |

### Amazon

| Part | Xavier | Orin | Quantity | Quantity per Package | Package Quantity | Link |
| --- | --- | ---- | --- | --- | --- | --- |
| SSD | X | X | 1 | 1 | 1 | [Link](https://www.amazon.ca/-/fr/Samsung970-interne-MZ-V7S250-AM-Version/dp/B07MG119KG) |
| USB 3.0 Hub | X | X | 2 | 1 | 2 | [Link](https://www.amazon.ca/-/fr/dp/B01M4J1DDP/ref=dp_prsubs_2?th=1) |
| Touchscreen | X | X | 1 | 1 | 1 | [Link](https://www.amazon.ca/Longruner-Capacitive-Display-800x480-Raspberry/dp/B071X8H5FB) |
| Limit Switch | X | X | 1 | 10 | 1 | [Link](https://www.amazon.ca/-/fr/InduSKY-micro-interrupteurs-course-levier-momentan%C3%A9/dp/B08736NP44/) |
| 270-Degree HDMI Adapter | X | X | 2 | 1 | 2 | [Link](https://www.amazon.ca/Monoprice-103850-Degree-Female-Saver/dp/B002K8H7XS) |
| Nvidia Jetson AGX Xavier | X | | 1 | 1 | 1 | [Link](https://www.amazon.ca/-/fr/NVIDIA-Jetson-AGX-Xavier-développeur/dp/B083ZL3X5B) |
| WiFi Card | X | | 1 | 1 | 1 | [Link](https://www.amazon.ca/Wireless-Card-2-4GHz-Intel-8265-NGW/dp/B07Q3NG5CZ) |
| Ethernet Cable | X | X | 1 | 1 | 1 | [Link](https://www.amazon.ca/-/fr/AmazonBasics-Câble-réseau-Ethernet-catégorie/dp/B00N2VISLW) |
| Mini-USB Cable | X | X | 1 | 1 | 1 | [Link](https://www.amazon.ca/-/fr/embarquée-appareils-numériques-navigation-satellite/dp/B00P0GI68M) |
| Micro-USB Cable - Right Angle | X | X | 1 | 1 | 1 | [Link](https://www.amazon.ca/-/fr/StarTech-Usbaub5cmd-Cordon-câble-micro/dp/B00EBGGXS2) |
| HDMI Cable (1.5 ft) | X | | 1 | 1 | 1 | [Link](https://www.amazon.ca/-/fr/Monoprice-113586-Ultra-Série-câble-vitesse/dp/B014ROO14U) |
| HDMI Cable (0.5 ft) | | X | 1 | 1 | 1 | [Link](https://www.amazon.ca/-/fr/dp/B014ROO71W/) |
| 90-Degree Display Port Adapter | | X | 1 | 1 | 1 | [Link](https://www.amazon.ca/dp/B07CMKWFS1) |
| Display Port to HDMI Adapter | | X | 1 | 2 | 1 | [Link](https://www.amazon.ca/dp/B089NP5J98) |
| 90-Degree USB-C Adapter | X | X | 1 | 1 | 1 | [Link](https://www.amazon.ca/-/fr/Adaptateur-femelle-extension-Chromebook-Pixelbook/dp/B07VN4SFWM) |
| 1/8-Inch Stereo Jack Cable | X | X | 2 | 1 | 2 | [Link](https://www.amazon.ca/-/fr/UGREEN-C%C3%A2ble-audio-auxiliaire-st%C3%A9r%C3%A9o/dp/B00LM0U8I6/) |
| 605zz Bearing | X | X | 9 | 10 | 1 | [Link](https://www.amazon.ca/-/fr/Generic-roulements-billes-miniatures-blindage/dp/B07VTKYF73) |
| Fan - Noctua NF-A4x20 | X | X | 2 | 1 | 2 | [Link](https://www.amazon.ca/Noctua-NF-A4x20-5V-Premium-Quality-Quiet/dp/B072Q3CMRW) |
| 16 AWG Wire | X | X | 1 | 1 | 1 | [Link](https://www.amazon.ca/Electrical-Gauge-Silicone-Cable-Black/dp/B0746HRVZP) |
| 20 AWG Wire | X | X | 1 | 1 | 1 | [Link](https://www.amazon.ca/-/fr/TUOFENG-Fil-%C3%A9lectrique-AWG-raccordement/dp/B07GBW32MR) |
| 22 AWG Wire | X | X | 1 | 1 | 1 | [Link](https://www.amazon.ca/-/fr/TUOFENG-Fil-électrique-AWG-raccordement/dp/B07G2JWYDW) |
| Heat Shrink Tube Kit | X | X | 1 | 1 | 1 | [Link](https://www.amazon.ca/-/fr/SummitLink%C2%AE-thermor%C3%A9tractables-assorties-couleurs-tailles/dp/B01EMHNTWC) |
| Ground Loop Noise Isolator | X | X | 2 | 1 | 2 | [Link](https://www.amazon.ca/Isolateur-élimine-bourdonnement-système-voiture/dp/B019FC6ZQQ) |
| 19V Power Adapter Wall Cable | X | X | 1 | 1 | 1 | [Link](https://www.amazon.ca/-/fr/AmazonBasics-C%C3%A2ble-dalimentation-rechange-dordinateur/dp/B072BYGKZZ/) |
| RJ12 Connector | X | X | 32 | 100 | 1 | [Link](https://www.amazon.ca/Uvital-Transparent-Telephone-Modular-Connector/dp/B07Z7VFLTC) |
| RJ12 Flat Cable | X | X | 1 | 1 | 1 | [Link](https://www.amazon.ca/-/fr/C%C3%A2ble-r%C3%A9seau-RJ-12-RJ-12-7-pieds-Argent/dp/B0002J1ST6) |
| Ferrules | X | X | 1 | 1 | 1 | [Link](https://www.amazon.ca/-/fr/Preciva-AWG23-10-sertissage-auto-r%C3%A9glable-connecteurs/dp/B081BSGHGY) |

### Aliexpress

| Part | Xavier | Orin | Quantity | Quantity per Package | Package Quantity | Link |
| --- | -----  | ---- | --- | --- | --- | --- |
| Ball Joint - M3 Silver | X | X | 12 | 20 | 1 | [Link](https://fr.aliexpress.com/item/1005004043955065.html) |
| Threaded Rod - M3x180mm | X | X | 6 | 10 | 1 | [Link](https://fr.aliexpress.com/item/1005004659556705.html) |
| Slip Ring - M220-24 36wire 2A flange A | X | X | 1 | 1 | 1 | [Link](https://fr.aliexpress.com/item/32919903199.html) |
| Battery Charger Connector - JST PHR-6  | X | X | 1 | 1 | 1 | [Link](https://fr.aliexpress.com/item/32963428352.html) |
| Magnets (5x2mm) | X | X | 46 | 50 | 1 | [Link](https://fr.aliexpress.com/item/1005001530691922.html) |
| LED Connectors (XH, 200mm, 3 pin) | X | X | 3 | 10 | 1 | [Link](https://fr.aliexpress.com/item/1005004015984711.html) |
| LED Strip (WS2812B, 5M, IP30, 30/m) | X | X | 1 | 1 | 1 | [Link](https://fr.aliexpress.com/item/1005004267050906.html) |
| LED Strip (WS2812B, 1M, IP30, 144/m) | X | X | 1 | 1 | 1 | [Link](https://fr.aliexpress.com/item/1005004267050906.html) |
| JST-XH Connector Kit | X | X | 1 | 1 | 1 | [Link](https://fr.aliexpress.com/item/1005003666557703.html) |
| JST-PH Connector Kit | X | X | 2 | 1 | 2 | [Link](https://fr.aliexpress.com/item/1005003666557703.html) |
| JST-PH Right Angle (3P) | X | X | 1 | 50 | 1 | [Link](https://fr.aliexpress.com/item/33053313994.html) |
| T-Connector Cable (female with cable)  | X | X | 1 | 1 | 1 | [Link](https://fr.aliexpress.com/item/1005003767214165.html) |

### Other

| Part | Xavier | Orin | Quantity | Quantity per Package | Package Quantity | Link |
| --- | --- | ---- | --- | --- | --- | --- |
| Speaker | X | X | 4 | 1 | 4 | [Link](https://solen.ca/products/speakers/home-speakers/fullranges/dayton-audio-dma45-8-1-1-2-dual-magnet-aluminum-cone-full-range-driver-8-ohm/) |
| Wide Angle Camera | X | X | 1 | 1 | 1 | [Link](https://www.uctronics.com/arducam-1080p-hd-wide-angle-wdr-usb-camera-module-for-computer-2mp-1-2-7-cmos-ar0230-100-degree-mini-uvc-usb2-0-spy-webcam-board-with-3-3ft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) |
| Wide Angle Camera Lens | X | X | 1 | 1 | 1 | [Link](https://www.uctronics.com/arducam-1-95mm-m12-lens-m27195h15-for-usb-camera.html) |
| Power Connector | X | X | 4 | 1 | 4 | [Link](https://addison-electronique.com/en/products/electricity/kit-of-housing-connectors-male-fem-2-pin-type-250/) |
| Battery Charger - RRC-PMM240 | X | X | 1 | 1 | 1 | [Link](https://www.mouser.ca/ProductDetail/RRC-Power-Solutions/RRC-PMM240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) |
| Battery - RRC2054-2 | X | X | 1 | 1 | 1 | [Link](https://www.mouser.ca/ProductDetail/RRC-Power-Solutions/RRC2054-2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) |
| 16SoundsUSB | X | X | 1 | 1 | 1 | [Link](https://github.com/introlab/16SoundsUSB) |
| xSoundsMicrophones | X | X | 16 | 1 | 16 | [Link](https://github.com/introlab/xSoundsMicrophones) |
| RTC Clock Battery | | X | 1 | 1 | 1 | [Link](https://rometechcases.com/products/rtc-cmos-battery-for-nvidia-jetson-agx-orin-developer-kit) |

## Bill of Materials of Custom PCBs

### PSU Control PCB

In order to assemble this PCB, you need to manufacture it. The Gerber files are
located [here](../../PCB/psu_control/gerber).

| #  | Quantity | Reference(s) | Value | Link |
| -- | --- | --- | --- | --- |
| 1  | 21 | C1, C7, C8, C11, C12, C13, C14, C15, C16, C17, C18, C19, C20, C21, C22, C25, C26, C27, C28, C29, C30 | 0.1µF/25V | [Link](https://www.digikey.ca/en/products/detail/samsung-electro-mechanics/CL21B104KACNNNC/3886757) |
| 2  | 1 | C2 | 22µF/25V | [Link](https://www.digikey.ca/en/products/detail/samsung-electro-mechanics/CL21A226MAYNNNE/10479857) |
| 3  | 1 | C3 | 1µF/10V | [Link](https://www.digikey.ca/en/products/detail/samsung-electro-mechanics/CL21B105KPFNNNE/3886933) |
| 4  | 2 | C4, C31 | 22μF/10V | [Link](https://www.digikey.ca/en/products/detail/samsung-electro-mechanics/CL21A226MPQNNNE/3888568) |
| 5  | 3 | C5, C9, C23 | 100µF/35V | [Link](https://www.digikey.ca/en/products/detail/kemet/ESH107M035AE3AA/3082962) |
| 6  | 1 | C6 | 680µF/35V | [Link](https://www.digikey.ca/en/products/detail/panasonic-electronic-components/EEU-FR1V681/2504783) |
| 7  | 2 | C10, C24 | 10µF/25V | [Link](https://www.digikey.ca/en/products/detail/samsung-electro-mechanics/CL21A106KAYNNNE/3888549) |
| 8  | 3 | D1, D2, D3 | DSS16U | [Link](https://www.digikey.ca/en/products/detail/smc-diode-solutions/DSS16U/8341861) |
| 9  | 2 | D4, D5 | White | [Link](https://www.digikey.ca/en/products/detail/lite-on-inc/LTW-2S3D8/2666499) |
| 10 | 1 | D6 | SMAJ9.0A-13-F | [Link](https://www.digikey.ca/en/products/detail/diodes-incorporated/SMAJ9-0A-13-F/775752) |
| 11 | 1 | D7 | SZ1SMA24AT3G | [Link](https://www.digikey.ca/en/products/detail/littelfuse-inc/SZ1SMA24AT3G/3062913) |
| 12 | 2 | F1 | Fuse Clip | [Link](https://www.digikey.ca/en/products/detail/keystone-electronics/3517/316010) |
| 13 | 1 | F1 | 10A Slow Blow | [Link](https://www.digikey.ca/en/products/detail/bel-fuse-inc/5STP-10-R/1010133) |
| 14 | 3 | J1, J2, J4 | OSTTA020161 | [Link](https://www.digikey.ca/en/products/detail/on-shore-technology-inc/OSTTA020161/614512) |
| 15 | 1 | J6 | LED Strip - 5m 30-LEDs IP30  | [Link](https://fr.aliexpress.com/item/1005004267050906.html) |
| 16 | 1 | J6 | LED Strip - 1m 144-LEDs IP30 | [Link](https://fr.aliexpress.com/item/1005004267050906.html) |
| 17 | 2 | L1, L2 | 22µH (NS12575T220MN) | [Link](https://www.digikey.ca/en/products/detail/taiyo-yuden/NS12575T220MN/2573847) |
| 18 | 1 | LS1 | CEM-1206S | [Link](https://www.digikey.ca/en/products/detail/cui-devices/CEM-1206S/412414) |
| 19 | 1 | Q2 | SUD50P04-09L-E3 | [Link](https://www.digikey.ca/en/products/detail/vishay-siliconix/SUD50P04-09L-E3/2623069) |
| 20 | 1 | Q3 | T2N7002AK | [Link](https://www.digikey.ca/en/products/detail/toshiba-semiconductor-and-storage/T2N7002AK-LM/5298028) |
| 21 | 1 | Q4 | DMG9926USD | [Link](https://www.digikey.ca/en/products/detail/diodes-incorporated/DMG9926USD-13/2179801) |
| 22 | 4 | R3, R4, R40, R41 | 2.2k | [Link](https://www.digikey.ca/en/products/detail/yageo/RC0805FR-072K2L/727676) |
| 23 | 5 | R5, R6, R13, R23, R24 | 100k | [Link](https://www.digikey.ca/en/products/detail/stackpole-electronics-inc/RMCF0805FT100K/1760712) |
| 24 | 2 | R9, R10 | 0 | [Link](https://www.digikey.ca/en/products/detail/stackpole-electronics-inc/RMCF0805ZT0R00/1756901) |
| 25 | 2 | R11, R12 | 10 | [Link](https://www.digikey.ca/en/products/detail/stackpole-electronics-inc/RMCF0805FT10R0/1760155) |
| 26 | 1 | R14 | 0.004 | [Link](https://www.digikey.ca/en/products/detail/rohm-semiconductor/PMR18EZPFV4L00/2094210) |
| 27 | 14 | R15, R18, R25, R26, R27, R28, R29, R30, R31, R32, R33, R34, R35, R36 | 10k | [Link](https://www.digikey.ca/en/products/detail/yageo/AC0805FR-0710KL/2827834) |
| 28 | 3 | R21, R22, R39 | 698 | [Link](https://www.digikey.ca/en/products/detail/yageo/RC0805FR-07698RL/728107) |
| 29 | 2 | R37, R38 | 63.4 | [Link](https://www.digikey.ca/en/products/detail/panasonic-electronic-components/ERJ-6ENF63R4V/111047) |
| 30 | 1 | R42 | 47 | [Link](https://www.digikey.ca/en/products/detail/yageo/RC0805FR-0747RL/727972) |
| 31 | 2 | R43, R44 | 0 | [Link](https://www.digikey.ca/en/products/detail/stackpole-electronics-inc/RMCF1206ZT0R00/1756906) |
| 32 | 1 | TH2 | 10k | [Link](https://www.digikey.ca/en/products/detail/epcos-tdk-electronics/B57421V2103J062/739863) |
| 33 | 1 | U2 | Teensy LC | [Link](https://www.pjrc.com/store/teensylc.html) |
| 34 | 0.2 | U2 | 2.54 mm Male Header | [Link](https://www.aliexpress.com/item/1005002577212594.html) |
| 35 | 0.2 | U2 | 2.54 mm Female Header | [Link](https://www.aliexpress.com/item/1005002577212594.html) |
| 36 | 1 | U3 | INA220 | [Link](https://www.digikey.ca/en/products/detail/texas-instruments/INA220BQDGSRQ1/3478090) |
| 37 | 1 | U4 | K7805-3AR3 | [Link](https://www.digikey.ca/en/products/detail/mornsun-america-llc/K7805-3AR3/13168239) |
| 38 | 1 | U5 | M74HC14YTTR | [Link](https://www.digikey.ca/en/products/detail/stmicroelectronics/M74HC14YTTR/4725940) |
| 39 | 1 | U6 | SN74LV1T34 | [Link](https://www.digikey.ca/en/products/detail/texas-instruments/SN74LV1T34DBVR/4555575) |
| 40 | 1 | U7 | SN65C3221E | [Link](https://www.digikey.ca/en/products/detail/texas-instruments/SN65C3221EPWR/1216598) |
| 41 | 1 | U8 | 74LVC2G34 | [Link](https://www.digikey.ca/en/products/detail/nexperia-usa-inc/74LVC2G34GV-125/1231596) |
| 42 | 1 | J6 | JST-XH Kit | [Link](https://fr.aliexpress.com/item/1005003666557703.html) |
| 43 | 2 | SW1, SW2, SW3, SW4, SW5, SW6, TH1, J7, J8, J11, J12, J13, J14, J15, J16, D4, D5, M1, M2 | JST-PH Kit | [Link](https://fr.aliexpress.com/item/1005003666557703.html) |

### Dynamixel Control PCB

In order to assemble this PCB, you need to manufacture it. The Gerber files are
located [here](../../PCB/dynamixel_control/gerber).

| #  | Quantity | Reference(s) | Value | Link |
| -- | --- | --- | --- | --- |
| 1  | 3 | C1, C3, C14 | 10µF/25V | [Link](https://www.digikey.ca/en/products/detail/samsung-electro-mechanics/CL21A106KAYNNNE/3888549) |
| 2  | 1 | C2 | 4.7µF/25V | [Link](https://www.digikey.ca/en/products/detail/samsung-electro-mechanics/CL21A475KAQNNNE/3886902) |
| 3  | 13 | C4, C5, C7, C8, C9, C10, C11, C13, C15, C18, C19, C22, C23 | 0.1µF/25V | [Link](https://www.digikey.ca/en/products/detail/samsung-electro-mechanics/CL21B104KACNNNC/3886757) |
| 4  | 1 | C6 | 10nF/25V | [Link](https://www.digikey.ca/en/products/detail/samsung-electro-mechanics/CL21B103KAANNNC/3888092) |
| 5  | 2 | C12, C25 | 2.2µF/25V | [Link](https://www.digikey.ca/en/products/detail/samsung-electro-mechanics/CL21B225KAFNNNE/3888612) |
| 6  | 1 | J1 | Male T-Connector | [Link](https://fr.aliexpress.com/item/1005001899904442.html) |
| 7  | 1 | J2 | JST-PH Right Angle 3 Positions | [Link](https://fr.aliexpress.com/item/33053313994.html) |
| 8  | 3 | J8, J11, J12 | Dynamixel Connector | [Link](https://www.digikey.ca/en/products/detail/adam-tech/25SH-C-03-TS/9830389) |
| 9  | 2 | L1, L2 | 12µH (RLS-126) | [Link](https://www.digikey.ca/en/products/detail/recom-power/RLS-126/9920565) |
| 10 | 1 | Q2 | IPD068P03L3GATMA1 | [Link](https://www.digikey.ca/en/products/detail/infineon-technologies/IPD068P03L3GATMA1/5334529) |
| 11 | 1 | Q3 | T2N7002AK | [Link](https://www.digikey.ca/en/products/detail/toshiba-semiconductor-and-storage/T2N7002AK-LM/5298028) |
| 12 | 4 | R1, R2, R3, R12 | 10k | [Link](https://www.digikey.ca/en/products/detail/yageo/AC0805FR-0710KL/2827834) |
| 13 | 3 | R4, R10, R11 | 0 | [Link](https://www.digikey.ca/en/products/detail/stackpole-electronics-inc/RMCF0805ZT0R00/1756901) |
| 14 | 2 | R7, R8 | 2.2k | [Link](https://www.digikey.ca/en/products/detail/yageo/RC0805FR-072K2L/727676) |
| 15 | 1 | R14 | 47 | [Link](https://www.digikey.ca/en/products/detail/yageo/RC0805FR-0747RL/727972) |
| 16 | 3 | R15, R16, R18 | 100k | [Link](https://www.digikey.ca/en/products/detail/stackpole-electronics-inc/RMCF0805FT100K/1760712) |
| 17 | 4 | R17 | 825 | [Link](https://www.digikey.ca/en/products/detail/yageo/RC0805FR-07825RL/728170) |
| 18 | 1 | SW1 | JST-PH Kit | [Link](https://fr.aliexpress.com/item/1005003666557703.html) |
| 19 | 1 | U1 | R-78E5.0-0.5 | [Link](https://www.digikey.ca/en/products/detail/recom-power/R-78E5-0-0-5/2834904) |
| 20 | 1 | U2 | SN74AHC1G14 | [Link](https://www.digikey.ca/en/products/detail/texas-instruments/SN74AHC1G14DBVR/276736) |
| 21 | 1 | U4 | Teensy 4.0 | [Link](https://www.pjrc.com/store/teensy40.html) |
| 22 | 0.2 | U4 | 2.54 mm Male Header | [Link](https://www.aliexpress.com/item/1005002577212594.html) |
| 23 | 0.2 | U4 | 2.54 mm Female Header | [Link](https://www.aliexpress.com/item/1005002577212594.html) |
| 24 | 1 | U5 | SN65C3221E | [Link](https://www.digikey.ca/en/products/detail/texas-instruments/SN65C3221EPWR/1216598) |
| 25 | 1 | U6 | ICM-40627 | [Link](https://www.mouser.ca/ProductDetail/TDK-InvenSense/ICM-40627?qs=iLbezkQI%252BsgePVjJNSY7vQ%3D%3D) |
| 26 | 1 | U7 | SN74LV1T34 | [Link](https://www.digikey.ca/en/products/detail/texas-instruments/SN74LV1T34DBVR/4555575) |
| 27 | 1 | U8 | SN74LVC2G241 | [Link](https://www.digikey.ca/en/products/detail/texas-instruments/SN74LVC2G241DCUR/389057) |

### Buck-Boost PCB

In order to assemble this PCB, you need to manufacture it. The Gerber files are
located [here](../../PCB/psu_control/gerber).

#### Common

The quantity of the following parts are for the 12V Buck-Boost PCB and 19V Buck-Boost PCB.

| #  | Quantity | Reference(s) | Value | Link |
| -- | --- | --- | --- | --- |
| 1  | 10 | C1, C2, C3, C11, C25  | 1000µF/35V | [Link](https://www.digikey.ca/en/products/detail/panasonic-electronic-components/EEU-FP1V102/9607229) |
| 2  | 8 | C5, C6, C7, C8 | 10µF/35V | [Link](https://www.digikey.ca/en/products/detail/samsung-electro-mechanics/CL31B106KLHNFNE/3888760) |
| 3  | 6 | C9, C18, C24 | 1µF/35V | [Link](https://www.digikey.ca/en/products/detail/taiyo-yuden/GMK212B7105MG-T/6563485) |
| 4  | 2 | C10 | 0.47µF/16V | [Link](https://www.digikey.ca/en/products/detail/samsung-electro-mechanics/CL21B474KOFNNNE/3886857) |
| 5  | 4 | C12, C16 | 2.2µF/16V | [Link](https://www.digikey.ca/en/products/detail/tdk-corporation/C2012X7R1C225K125AB/569046) |
| 6  | 2 | C13 | 220nF/16V | [Link](https://www.digikey.ca/en/products/detail/kemet/C0805C224K4RAC7210/12701375) |
| 7  | 2 | C14 | 27nF/16V | [Link](https://www.digikey.ca/en/products/detail/yageo/CC0805KRX7R9BB273/302873) |
| 9  | 2 | C17 | 4.7µF/16V | [Link](https://www.digikey.ca/en/products/detail/tdk-corporation/CGA4J3X7R1C475K125AB/2672862) |
| 10 | 2 | C19 | 470µF/35V | [Link](https://www.digikey.ca/en/products/detail/panasonic-electronic-components/EEU-TP1V471/2757714) |
| 11 | 8 | C20, C21, C22, C23 | 22µF/35V | [Link](https://www.digikey.ca/en/products/detail/tdk-corporation/C3216JB1V226M160AC/3948975) |
| 12 | 4 | D2, D3 | SS2040LL | [Link](https://www.digikey.ca/en/products/detail/panjit-international-inc/SS2040LL-R1-00001/14660534) |
| 13 | 2 | D5 | LED | [Link](https://www.digikey.ca/en/products/detail/dialight/5973305607F/2432541) |
| 14 | 10 | J1, J2, J3, J4, J5 | Terminal Block 2 Position | [Link](https://www.digikey.ca/en/products/detail/on-shore-technology-inc/OSTTA020161/614512) |
| 15 | 2 | L1 | 15µH | [Link](https://www.digikey.ca/en/products/detail/bourns-inc/PQ2617BHA-150K/7695916) |
| 16 | 2 | L2 | 1µH | [Link](https://www.digikey.ca/en/products/detail/pulse-electronics/PA4987-102HLT/13168607) |
| 16 | 8 | Q2, Q3, Q4, Q5 | TK1R4S04PB | [Link](https://www.digikey.ca/en/products/detail/toshiba-semiconductor-and-storage/TK1R4S04PB-LXHQ/12154999) |
| 17 | 2 | R1 | 412k | [Link](https://www.digikey.ca/en/products/detail/vishay-dale/CRCW0805412KFKEA/1175959) |
| 18 | 2 | R2 | 80.6k | [Link](https://www.digikey.ca/en/products/detail/panasonic-electronic-components/ERJ-6ENF8062V/111769) |
| 19 | 2 | R3 | 0.003/1W | [Link](https://www.digikey.ca/en/products/detail/stackpole-electronics-inc/CSNL1206FT3L00/1788092) |
| 20 | 2 | R4 | 12k | [Link](https://www.digikey.ca/en/products/detail/stackpole-electronics-inc/RMCF0805FT12K0/1760674) |
| 21 | 2 | R5 | 309k | [Link](https://www.digikey.ca/en/products/detail/panasonic-electronic-components/ERJ-6ENF3093V/112007) |
| 22 | 6 | R6, R8, R10 | 10k | [Link](https://www.digikey.ca/en/products/detail/yageo/RC0805FR-0710KL/727535) |
| 23 | 2 | R11 | 301 | [Link](https://www.digikey.ca/en/products/detail/stackpole-electronics-inc/RMCF0805FT301R/1760589) |
| 24 | 2 | R12 | 0 | [Link](https://www.digikey.ca/en/products/detail/stackpole-electronics-inc/HCJ1206ZT0R00/4357662) |
| 25 | 2 | RV2 | 20k | [Link](https://www.digikey.ca/en/products/detail/bourns-inc/3296W-1-203LF/1088051) |
| 26 | 2 | U2 | LT8392 | [Link](https://www.digikey.ca/en/products/detail/analog-devices-inc/LT8392HFE-PBF/13532451) |

#### 12V

Additionally, the 12V Buck-Boost PCB needs the following parts.

| #  | Quantity | Reference(s) | Value | Link |
| -- | --- | --- | --- | --- |
| 27 | 1 | C4 | 47nF/35V | [Link](https://www.digikey.ca/en/products/detail/samsung-electro-mechanics/CL21B473KBCNNNC/3886908) |
| 28 | 1 | Q1 | TK1R4S04PB  | [Link](https://www.digikey.ca/en/products/detail/toshiba-semiconductor-and-storage/TK1R4S04PB-LXHQ/12154999)  |
| 29 | 1 | R7 | 0,005/1W | [Link](https://www.digikey.ca/en/products/detail/rohm-semiconductor/PMR18EZPFU5L00/2094203) |
| 30 | 1 | R9 | 95.3k | [Link](https://www.digikey.ca/en/products/detail/panasonic-electronic-components/ERA-6AEB9532V/2025842) |
| 31 | 1 | RV1 | V27ZA2P | [Link](https://www.digikey.ca/en/products/detail/littelfuse-inc/V27ZA2P/1009448) |
| 32 | 1 | U1 | LTC4359-MS8 | [Link](https://www.digikey.ca/en/products/detail/analog-devices-inc/LTC4359CMS8-PBF/3306821) |

#### 19V

Additionally, the 19V Buck-Boost PCB needs the following parts.

| #  | Quantity | Reference(s) | Value | Link |
| -- | --- | --- | --- | --- |
| 27 | 1 | JP1 | Jumper | [Link](https://www.digikey.ca/en/products/detail/stackpole-electronics-inc/HCJ1206ZT0R00/4357662)  |
| 28 | 1 | R7 | 0,008/1W | [Link](https://www.digikey.ca/en/products/detail/rohm-semiconductor/PMR18EZPFU8L00/2094206) |
| 29 | 1 | R9 | 165k | [Link](https://www.digikey.ca/en/products/detail/yageo/RC0805FR-07165KL/727632) |

# 3D Printing

In order to assemble the robot, you need to 3D print the following parts that are located [here](../../CAD/STL).

| File | Xavier | Orin | Wall Thickness | Infill Percentage | Quantity |
| --- | --- | ---- | --- | --- | --- |
| [battery holder](../../CAD/STL/battery%20holder.STL) | X | X | 1.2 mm | 25 % | 1 |
| [base audio front left](../../CAD/STL/base%20audio%20front%20left.STL) | X | X | 1.2 mm | 25 % | 1 |
| [base audio front right](../../CAD/STL/base%20audio%20front%20right.STL) | X | X | 1.2 mm | 25 % | 1 |
| [base audio back left](../../CAD/STL/base%20audio%20back%20left.STL) | X | X | 1.2 mm | 25 % | 1 |
| [base audio back right](../../CAD/STL/base%20audio%20back%20right.STL) | X | X | 1.2 mm | 25 % | 1 |
| [base mic](../../CAD/STL/base%20mic.STL) | X | X | 1.2 mm | 25 % | 4 |
| [base gear 1](../../CAD/STL/base%20gear%201.STL) | X | X | 1.2 mm | 25 % | 1 |
| [base gear 2](../../CAD/STL/base%20gear%202.STL) | X | X | 1.2 mm | 25 % | 1 |
| [base gear 3](../../CAD/STL/base%20gear%203.STL) | X | X | 1.2 mm | 25 % | 1 |
| [base gear 4](../../CAD/STL/base%20gear%204.STL) | X | X | 1.2 mm | 25 % | 1 |
| [torso bottom external 1](../../CAD/STL/torso%20bottom%20external%201.STL) | X | X | 1.2 mm | 25 % | 1 |
| [torso bottom external 2](../../CAD/STL/torso%20bottom%20external%202.STL) | X | X | 1.2 mm | 25 % | 1 |
| [torso bottom external 3](../../CAD/STL/torso%20bottom%20external%203.STL) | X | X | 1.2 mm | 25 % | 1 |
| [torso bottom internal xavier](../../CAD/STL/torso%20bottom%20internal%20xavier.STL) | X | | 2.0 mm | 35 % | 1 |
| [torso bottom internal orin](../../CAD/STL/torso%20bottom%20internal%20orin.STL) | | X | 2.0 mm | 35 % | 1 |
| [torso bottom holder](../../CAD/STL/torso%20bottom%20holder.STL) | X | X | 1.2 mm | 25 % | 3 |
| [limit switch bracket](../../CAD/STL/limit%20switch%20bracket.STL) | X | X | 1.2 mm | 25 % | 1 |
| [stewart stand](../../CAD/STL/stewart%20stand.STL) | X | X | 1.2 mm | 25 % | 3 |
| [gear servo bracket](../../CAD/STL/gear%20servo%20bracket.STL) | X | X | 1.2 mm | 25 % | 1 |
| [torso bottom gear](../../CAD/STL/torso%20bottom%20gear.STL) | X | X | 1.2 mm | 25 % | 1 |
| [torso bottom magnet bracket](../../CAD/STL/torso%20bottom%20magnet%20bracket.STL) | X | X | 1.2 mm | 25 % | 1 |
| [stewart bottom 1](../../CAD/STL/stewart%20bottom%201.STL) | X | X | 1.2 mm | 25 % | 1 |
| [stewart bottom 2](../../CAD/STL/stewart%20bottom%202.STL) | X | X | 1.2 mm | 25 % | 1 |
| [stewart bottom 3](../../CAD/STL/stewart%20bottom%203.STL) | X | X | 1.2 mm | 25 % | 1 |
| [stewart horn left M3](../../CAD/STL/stewart%20horn%20left%20M3.STL) | X | X | 1.2 mm | 25 % | 1 |
| [stewart horn left M2.5](../../CAD/STL/stewart%20horn%20left%20M2.5.STL) | X | X | 1.2 mm | 25 % | 2 |
| [stewart horn right M3](../../CAD/STL/stewart%20horn%20right%20M3.STL) | X | X | 1.2 mm | 25 % | 1 |
| [stewart horn right M2.5](../../CAD/STL/stewart%20horn%20right%20M2.5.STL) | X | X | 1.2 mm | 25 % | 2 |
| [USB hub bracket](../../CAD/STL/USB%20hub%20stand.STL) | X | X | 1.2 mm | 25 % | 4 |
| [stewart top](../../CAD/STL/stewart%20top.STL) | X | X | 1.2 mm | 25 % | 1 |
| [head](../../CAD/STL/head.STL) | X | X | 1.2 mm | 25 % | 1 |
| [head cable protector](../../CAD/STL/head%20cable%20protector.STL) | X | X | 1.2 mm | 25 % | 1 |

# CNC/Laser Cutting

In order to assemble the robot, you need to cut the following parts out of 6 mm acrylic. The files are
located [here](../../CAD/DXF).

| File | Material | Thickness | Quantity | Notes |
| --- | --- | --- | --- | --- |
| [base disk](../../CAD/DXF/base%20disk.DXF) | Acrylic  | 6 mm | 1 | The counterboring depth is 4 mm. |

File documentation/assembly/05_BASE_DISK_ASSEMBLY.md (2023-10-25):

# 5. Base Disk Assembly

## A. Base Disk Pre-Assembly

### Required Parts

| Part | Quantity | Image |
|---| --- |---|
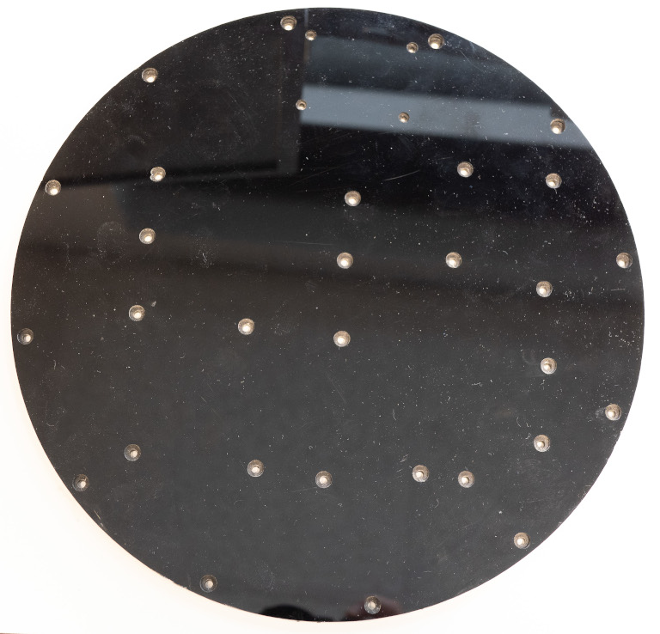
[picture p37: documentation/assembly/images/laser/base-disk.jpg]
Base Disk
| `Base Disk` | 1 |  |
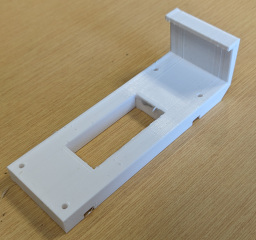
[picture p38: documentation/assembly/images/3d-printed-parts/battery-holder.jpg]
Battery Holder
| `Battery Holder` | 1 |  |
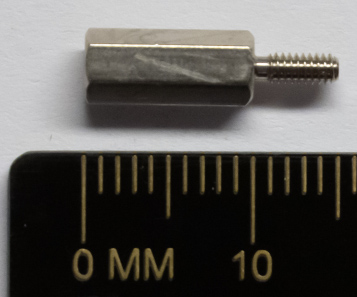
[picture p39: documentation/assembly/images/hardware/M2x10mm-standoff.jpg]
M2x10mm Standoff
| `M2x10mm Standoff` | 4 |  |
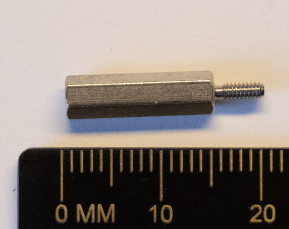
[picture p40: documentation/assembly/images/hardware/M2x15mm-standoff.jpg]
M2x15mm Standoff
| `M2x15mm Standoff` | 4 |  |
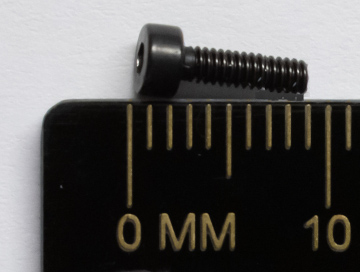
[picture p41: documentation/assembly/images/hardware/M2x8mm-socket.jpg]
M2x8mm Socket Screw
| `M2x8mm Socket Screw` | 4 |  |
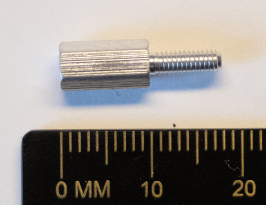
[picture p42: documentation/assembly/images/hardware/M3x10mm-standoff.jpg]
M2x10mm Standoff
| `M3x10mm Standoff` | 10 |  |
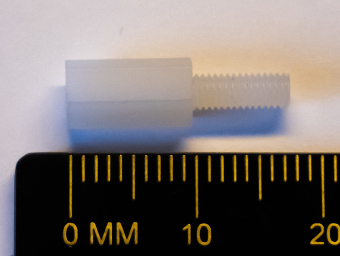
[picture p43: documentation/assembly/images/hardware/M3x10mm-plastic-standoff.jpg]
M2x10mm Standoff
| `M3x10mm Plastic Standoff` | 4 |  |
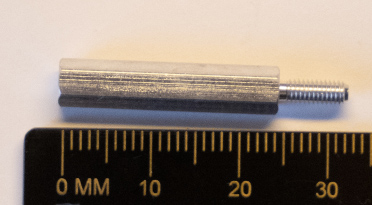
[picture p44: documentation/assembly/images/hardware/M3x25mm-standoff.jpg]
M2x10mm Standoff
| `M3x25mm Standoff` | 4 |  |
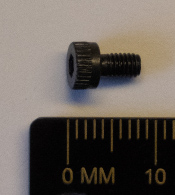
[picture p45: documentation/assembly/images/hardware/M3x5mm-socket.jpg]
M3x5mm Socket Screw
| `M3x5mm Socket Screw` | 14 |  |
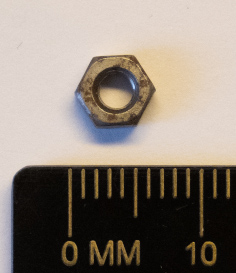
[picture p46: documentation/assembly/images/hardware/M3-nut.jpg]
M3 Nuts
| `M3 Nuts` | 6 |  |
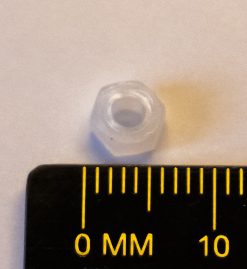
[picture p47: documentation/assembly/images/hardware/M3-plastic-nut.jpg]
M3 Plastic Nuts
| `M3 Plastic Nuts` | 4 |  |
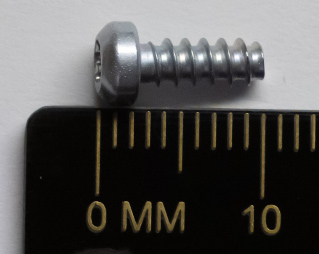
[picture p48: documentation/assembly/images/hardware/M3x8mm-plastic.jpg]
M3x8mm Plastic Screw
| `M3x8mm Plastic Screw` | 4 |  |
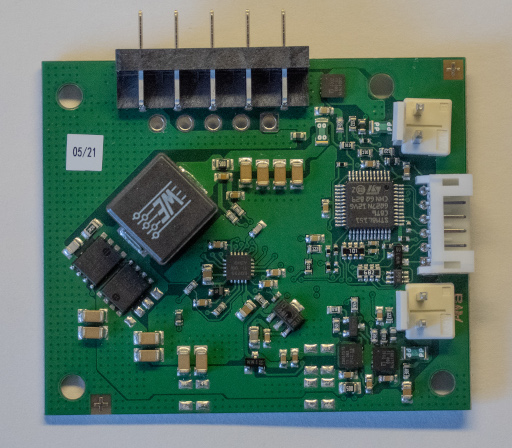
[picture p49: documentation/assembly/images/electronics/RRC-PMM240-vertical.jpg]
| `Battery Charger` | 1 |  |
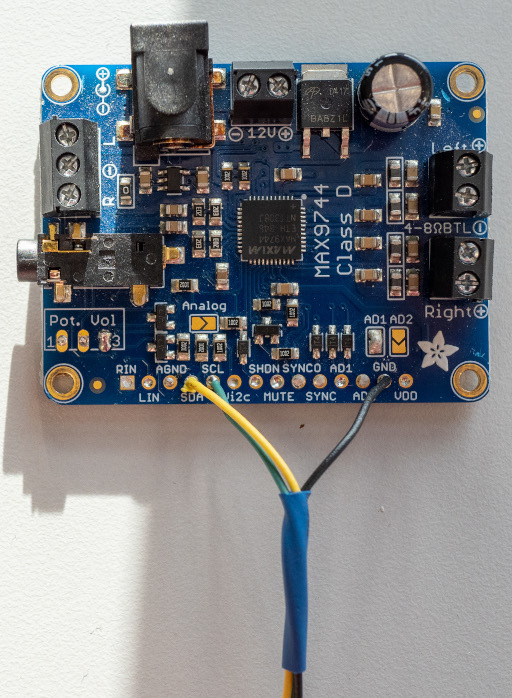
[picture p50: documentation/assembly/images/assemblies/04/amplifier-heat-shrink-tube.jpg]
| `Adafruit MAX9744` | 1 |  |
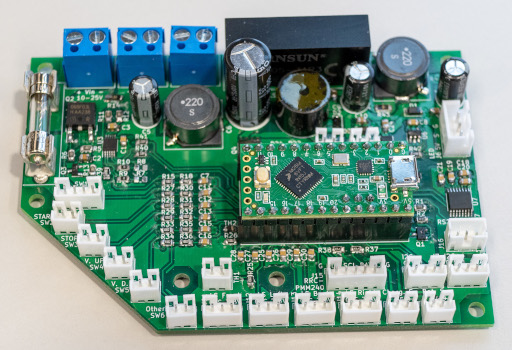
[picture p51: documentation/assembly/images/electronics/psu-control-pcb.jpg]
PSU Control PCB
| `PSU Control PCB` | 1 |  |
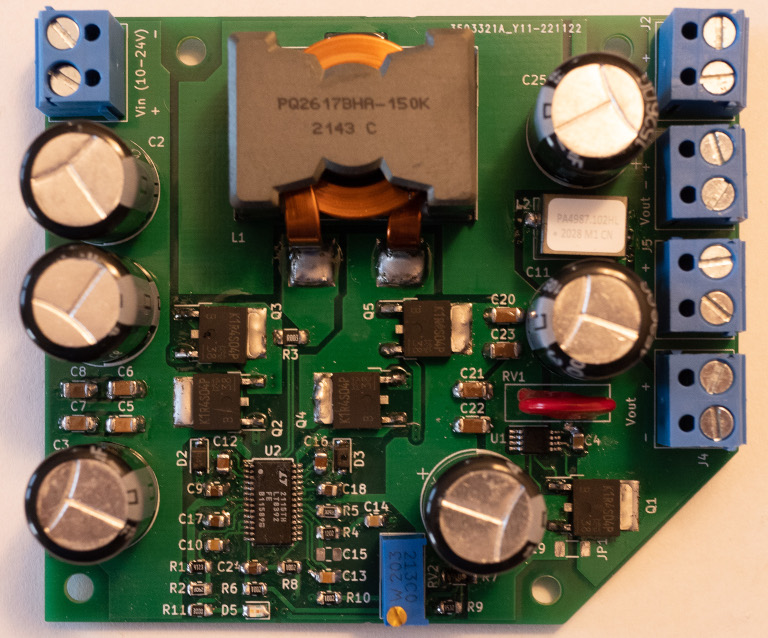
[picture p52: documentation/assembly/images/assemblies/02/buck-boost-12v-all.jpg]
12V Buck-Boost PCB
| `12V Buck-Boost PCB` | 1 |  |
| `14-cm-Long 16 AWG Red Wire` | 1 | `14-cm-long 16 AWG Red Wire |
| `14-cm-Long 16 AWG Black Wire` | 1 | `14-cm-long 16 AWG Black Wire |
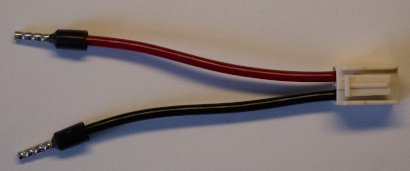
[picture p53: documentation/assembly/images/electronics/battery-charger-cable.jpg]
| `8-cm-Long JST VHR-2N Cable` | 1 |  |

### Steps

1. Install the `M2x10mm standoffs` with `M2x8mm socket screws` onto the `base disk`, as shown in the following pictures.

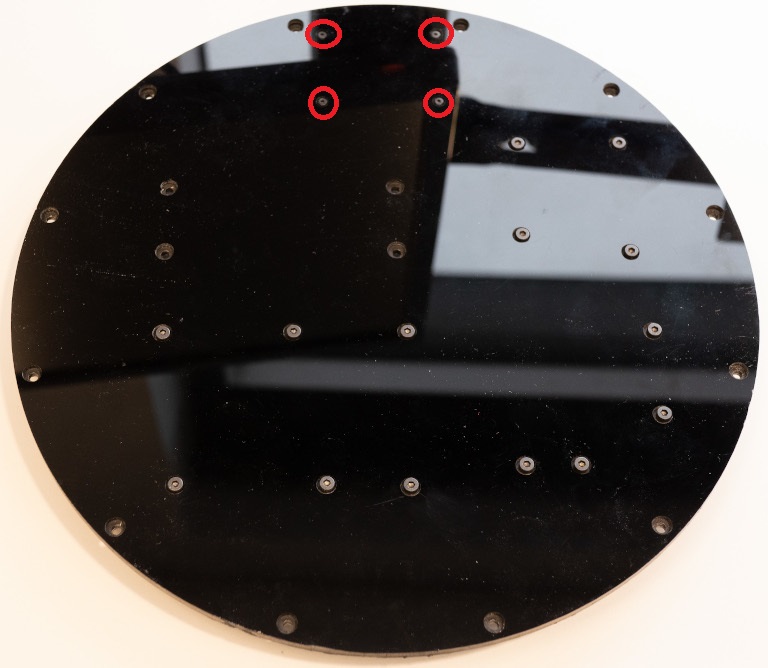
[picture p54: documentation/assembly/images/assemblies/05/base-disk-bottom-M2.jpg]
Base Disk Bottom M2

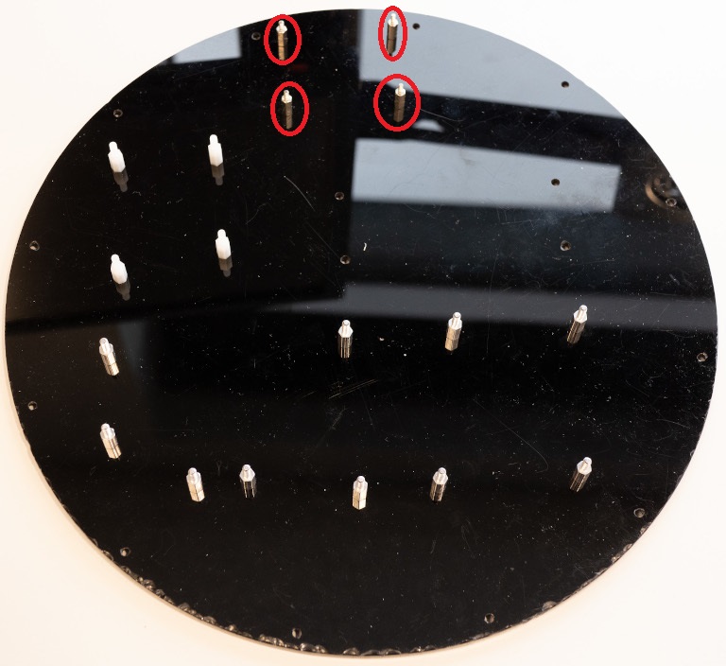
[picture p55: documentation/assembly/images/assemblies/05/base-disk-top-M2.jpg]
Base Disk Bottom M2


2. Install the `M3x10mm standoffs` with `M3x5mm socket screws` onto the `base disk`, as shown in the following pictures.

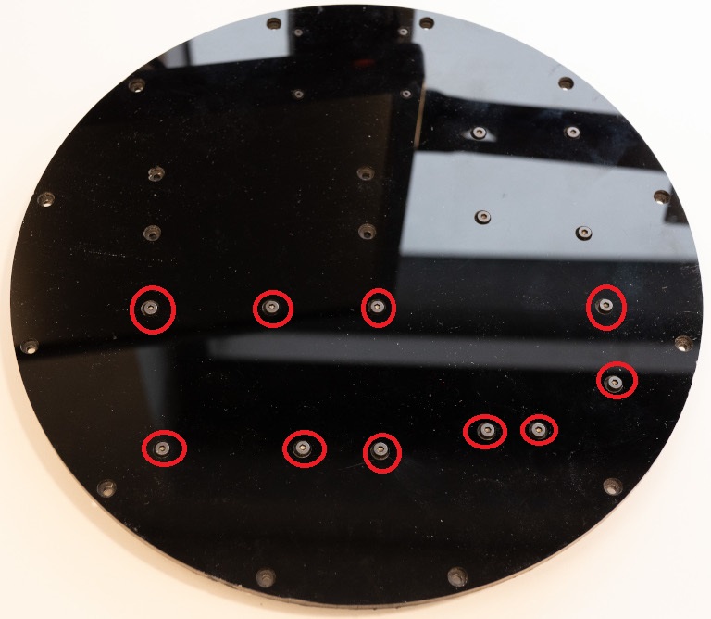
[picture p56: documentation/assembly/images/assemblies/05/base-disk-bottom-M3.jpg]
Base Disk Bottom M3

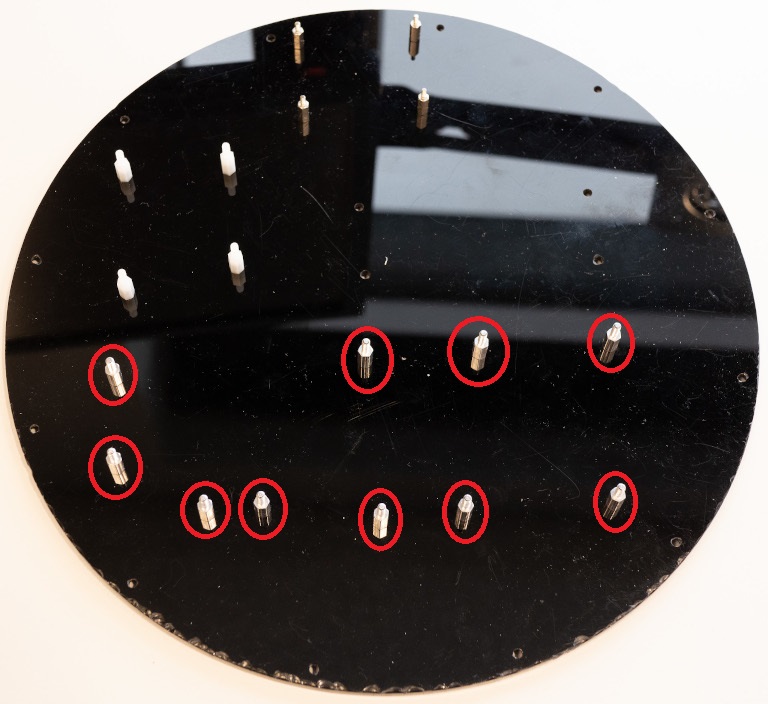
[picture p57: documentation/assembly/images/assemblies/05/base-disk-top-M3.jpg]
Base Disk Bottom M3


3. Install the `M3x10mm plastic standoffs` with `M3x5mm socket screws` onto the `base disk`, as shown in the following
   pictures.

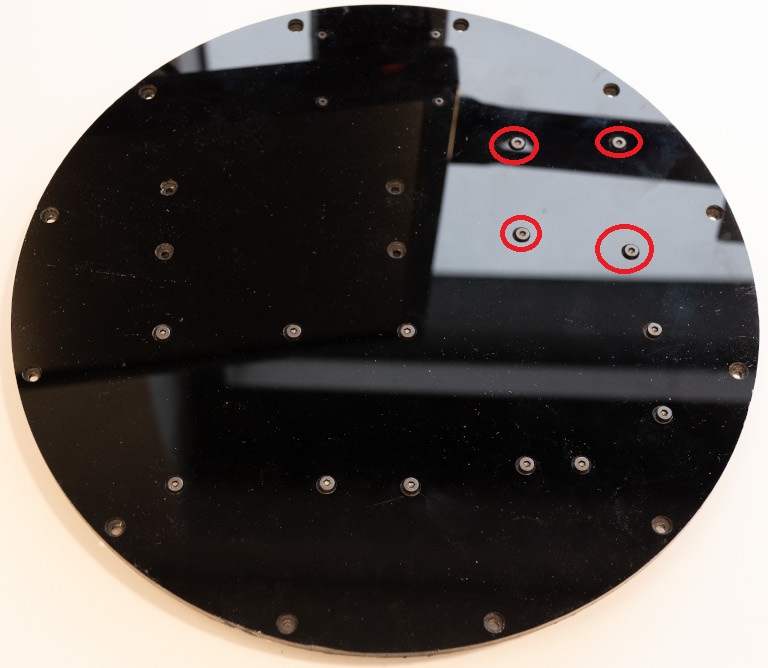
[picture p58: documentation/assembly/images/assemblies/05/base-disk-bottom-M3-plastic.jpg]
Base Disk Bottom M3 Plastic

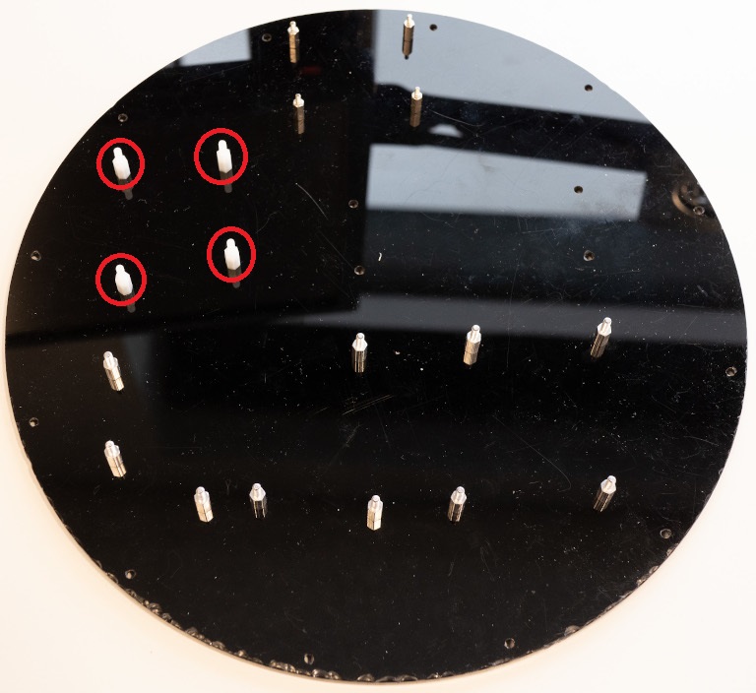
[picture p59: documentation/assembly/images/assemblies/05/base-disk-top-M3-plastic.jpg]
Base Disk Bottom M3 Plastic


4. Install the `battery holder` with `M3x8mm plastic screws` onto the `base disk`, as shown in the following pictures.

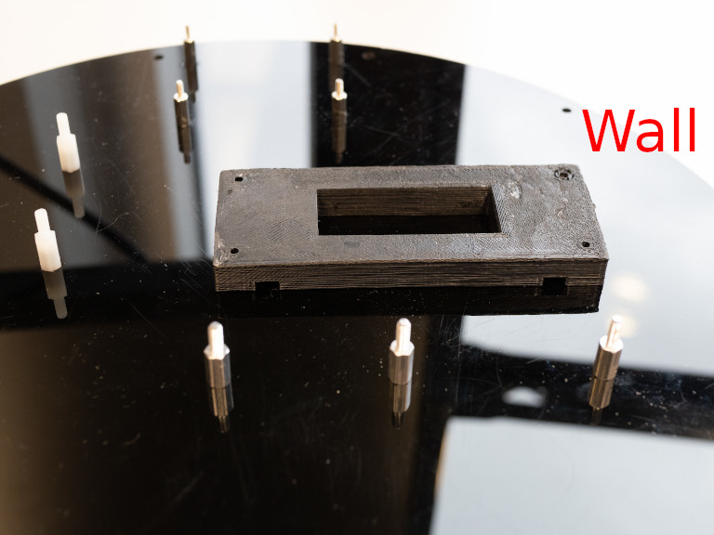
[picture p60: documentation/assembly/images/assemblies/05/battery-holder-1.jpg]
Battery Holder 1

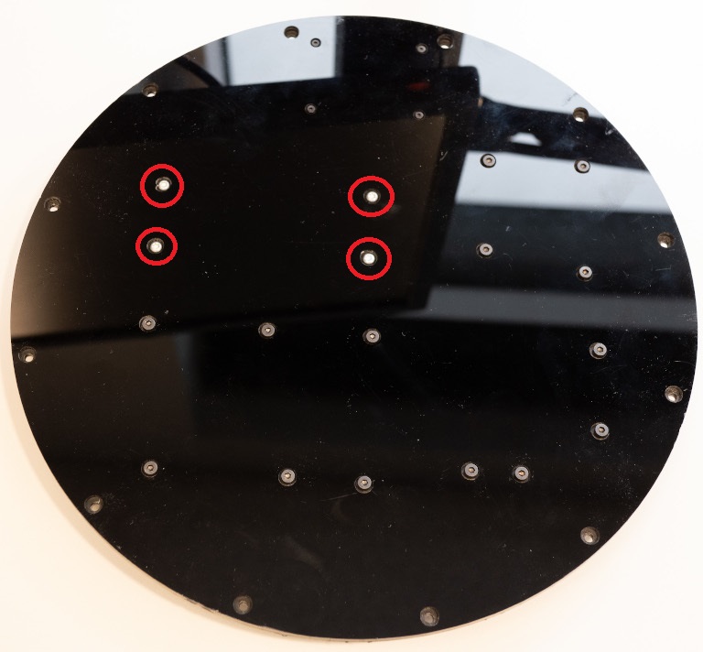
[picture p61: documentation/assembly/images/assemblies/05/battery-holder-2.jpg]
Battery Holder 2


5. Install the `battery charger` with `M3 plastic nuts`, as shown in the following picture.

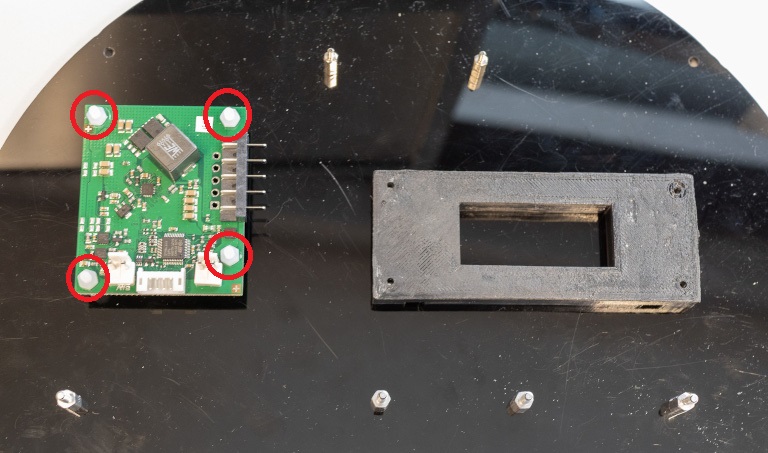
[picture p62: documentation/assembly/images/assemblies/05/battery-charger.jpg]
Battery Charger


6. Install the `Adafruit MAX9744` with `M2x15mm standoffs`, as shown in the following picture.

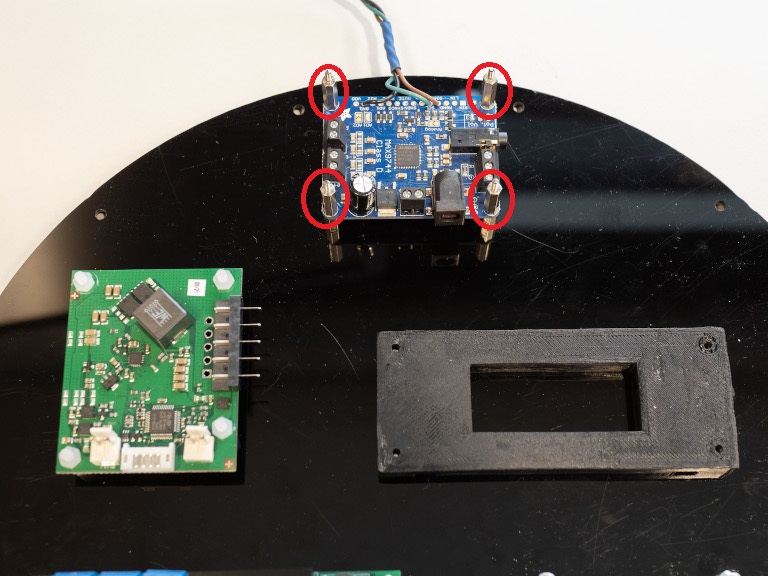
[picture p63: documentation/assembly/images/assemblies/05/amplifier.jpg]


7. Install the `PSU Control PCB`  with `M3 nuts`, as shown in the following picture.

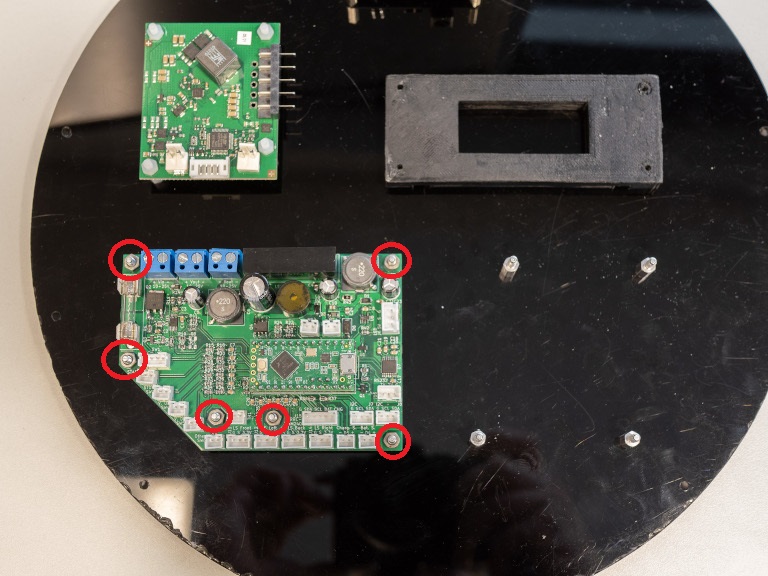
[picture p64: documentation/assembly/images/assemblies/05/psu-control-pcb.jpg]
PSU Control PCB


8. Install the `12V Buck-Boost PCB`  with a `M3 nut` (orange circle) and `M3x25mm standoffs` (red circles), as shown in
   the following picture.

12V Buck-Boost PCB

9. Connect the `12V Buck-Boost PCB` input to a `PSU control PCB` output with `14-cm-long 16 AWG wires`, as shown in the
   following picture.

12V Buck-Boost PCB Wires

10. Connect the `battery charger` to the `PSU control PCB` with the `8-cm-long JST VHR-2N cable`, as shown in the
    following picture.

Battery Charger Cable

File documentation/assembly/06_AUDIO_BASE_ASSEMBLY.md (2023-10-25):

# 6. Audio Base Assembly

## A. Audio Base Pre-Assembly

### Required Parts

| Part | Quantity | Image |
|---|---|---|
| `Base Audio Front Left` | 1 | Base Audio Front Left |
| `Base Audio Front Right` | 1 | Base Audio Front Right |
| `Base Audio Back Left` | 1 | Base Audio Back Left |
| `Base Audio Back Right` | 1 | Base Audio Back Right |
| `Dowel Pin` | 2 | Dowel Pin |
| `Magnet` | 16 | Magnet |
| `Assembled Speaker` | 4 | Assembled Speaker |
| `Assembled Fan` | 2 | Assembled Fan |
| `Micro USB Connector` | 1 | Micro USB Connector |
| `Assembled Power Switch` | 1 | Assembled Power Switch |
| `Ethernet Connector` | 1 | Ethernet Connector |
| `Assembled Robot Power Connector - Female` | 1 | Assembled Robot Power Connector - Female |
| `Assembled White LED` | 2 | Assembled LED |
| `M3x8mm Plastic Screw` | 22 | M3x8mm Plastic Screw |
| `Fan Screw` | 8 | Fan Screw |
| `Assembled Push Button` | 4 | Assembled Push Button |
| `Assembled Light Sensor` | 4 | Assembled Light Sensor |
| `M2x5mm Plastic Screw` | 4 | M2x5mm Plastic Screw |

### Steps
1. Install four `magnets` with super glue into the dedicated holes on each of the `base audio front left`, `base audio front right`, `base audio back left`, `base audio back right` parts, as shown in the following pictures.

Base Audio Parts Magnets
Base Audio Parts Magnets
Base Audio Parts Magnets
Base Audio Parts Magnets

2. Install dowel pins on `base audio back left` part, as shown in the following picture.

Base Audio Parts Dowel Pins

3. Insert the `base audio front left` part into the `base audio front right`, then insert `base audio back left` part into the `base audio back right` to form the full circular base, as shown in the following picture.

Base Audio Parts

4. Put 6 `M3x8 plastic screws` to fix the parts together, as shown in the following pictures.

Base Audio Screw 1
Base Audio Screw 2
Base Audio Screw 3

3. Install the `assembled speakers` with `M3x8 plastic screws`, as shown in the following pictures. The wire lengths are
   shown in the picture.

Base Audio Speaker 1

Base Audio Speaker 2

4. Install the `assembled fans` with `fan screws`, as shown in the following pictures.

Base Audio Fan 1
Base Audio Fan 2

5. Install the `Micro USB connector` as shown in the following picture.

Base Audio Micro USB

6. Install the `assembled power switch` as shown in the following picture.

Base Audio Power Switch

7. Install the `assembled push buttons` as shown in the following picture.

Base Audio Push Buttons

8. Install the `assembled robot power connector` with epoxy glue, as shown in the following picture.

Base Audio Power Connector

9. Install the `assembled white LEDs` with epoxy glue, as shown in the following picture.

Base Audio LEDs

10. Install the `light sensors` with `M2x5 plastic screws`, as shown in the following pictures.

Base Audio Light Sensors 1

Base Audio Light Sensors 2

Base Audio Light Sensors 3

Base Audio Light Sensors 4

## B. Audio Base Assembly

### Required Parts

| Part | Quantity | Image |
| --- | --- | --- |
| `Audio Base Pre-Assembly` | 1 | |
| `Base Disk Pre-Assembly` | 1 | |
| `M3x8mm Plastic Screw` | 12 | M3x8mm Plastic Screw |
| `Adafruit MAX9744` | 1 | Adafruit MAX9744 |
| `M2 Nuts` | 4 | M3 Nuts |
| `Assembled JST PHR-6 Cable` | 1 | |
| `Female Power Connector with Ferrules` | 1 | Power Connector - Female |
| `19V Buck-Boost PCB` | 1 | 19V Buck-Boost PCB |
| `M3 Nuts` | 3 | M3 Nuts |
| `8-cm-Long 16 AWG Red Wire` | 1 | `8-cm-long 16 AWG Red Wire |
| `8-cm-Long 16 AWG Black Wire` | 1 | `8-cm-long 16 AWG Black Wire |
| `Male Power Connector with Ferrules` | 1 | Power Connector - Male |
| `Assembled LED Strip` | 3 | |

### Steps

1. Install the `base disk pre-assembly` onto the `audio base pre-assembly` with `M3x8mm plastic screws`, as shown in the following picture.

Base Disk

2. Connect the `fans` as shown in the following picture.

Fans

3. Connect the push buttons as show in the following picture. Make sure each button is connected to the right place.

Fans

4. Connect the `power switch` as shown in the following picture.

Power Switch

5. Connect the `light sensors`as shown in the following picture. Make sure you connect the front, left, back, right sensor at the right place.

Light sensors

6. Install the `LED strips` and use the underneath adhesive to stick with the base, as shown in the following picture:

LED Strips

7. Connect the `LED strips` as shown in the following picture.

LED Strips Connector

10. Install the `Ethernet connector` as shown in the following picture.

Base Audio Ethernet

11. Connect the `assembled robot power connector` as shown in the following picture.

Power Connector

12. Connect the `PSU control PCB` to the `battery charger` with the `assembled JST PHR-6 cable`, as shown in the
    following picture.

JST PHR-6 Cable

13. Connect the `assembled white LEDs` as shown in the following picture. The LED labelled "PSU" is connected to the connector labelled "Charg. S.".

White LEDs

14. Connect the `Micro USB connector` as shown in the following picture.

Micro USB connector

15. Connect 2 `25-cm long 20 AWG Adafruit MAX9744 wires` to the `12V Buck-Boost PCB`, as shown in the following picture.

Adafruit MAX9744 Wires 1

16. Connect those wires to the `Adafruit MAX9744`, as shown in the following picture.

Adafruit MAX9744 Wires 2

17. Connect the `farthest speakers` to the `Adafruit MAX9744`, as shown in the following picture.

Adafruit MAX9744 Wires 3

18. Install the second `Adafruit MAX9744` onto the top of the first one with `M2 nuts`, as shown in the following
   picture.

Adafruit MAX9744

19. Connect 2 `25-cm long 20 AWG Adafruit MAX9744 wires` to the `12V Buck-Boost PCB`, as shown in the following picture.

Adafruit MAX9744 Wires 4

20. Connect those wires to the second `Adafruit MAX9744`, as shown in the following picture.

Adafruit MAX9744 Wires 5

21. Connect the `nearest speakers` to the second `Adafruit MAX9744`, as shown in the following picture.

Adafruit MAX9744 Wires 6

22. Connect the `Adafruit MAX9744 I2C cables` to the `PSU control PCB`, as shown in the following picture.

Amplifier

23. Secure the wires with tie wraps as shown in the following picture.

Tie Wraps

24. Connect the `female power connector with ferrules` to a `12V Buck-Boost PCB` output.

25. Install the `19V Buck-Boost PCB`  with `M3 nuts` (orange circle), as shown in the following picture.

19V Buck-Boost PCB

26. Connect the `19V Buck-Boost PCB` input to a `PSU control PCB` output with `8-cm-long 16 AWG wires`, as shown in the
    following picture.

19V Buck-Boost PCB Wires

27. Connect the `male power connector with ferrules` to a `19V Buck-Boost PCB` output.

## C. Setup the Battery Charger

### Required Parts

| Part | Quantity | Image |
| --- | --- | --- |
| `Micro USB Cable` | 1 | |
| `19V Power Adapter` | 1 | |

### Steps

1. Open the [project](../../firmwares/psu_control) in PlatformIO.
2. Change the value `FIRMWARE_MODE` in [config.h](../../firmwares/psu_control/src/config.h)
   to `FIRMWARE_MODE_SETUP_BATTERY_CHARGER`.
3. Make sure the battery is removed.
4. Connect the micro USB cable to the computer and the Teensy LC.
5. Turn off the robot.
6. Connect the `19V Power Adapter` to the base.
7. Turn on the robot.
8. Click on the upload button.

## D. Finish the Audio Base Assembly

### Required Parts

| Part | Quantity | Image |
| --- | --- | --- |
| `Battery - RRC2054-2` | 1 | Battery - RRC2054-2 |
| `Ground Loop Noise Isolator` | 2 | Ground Loop Noise Isolator |
| `Diffuser Plastic Sheet` | 1 | |

### Steps

1. Install the `battery` and the `ground loop noise isolators` with tie wraps, as shown in the following picture.

Battery

2. Connect the `ground loop noise isolators` to the `Adafruit MAX9744`.

3. Cut the LED diffusers according to the groove dimensions.
    - 16 mm x 48 mm (2x)
    - 13 mm x 530 mm (2x)
4. Sand the back of the LED diffusers.
5. Install the LED diffusers with super glue.

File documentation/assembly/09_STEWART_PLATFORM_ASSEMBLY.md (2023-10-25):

# 9. Stewart Platform Assembly

## A. Dynamixel Centering

### Required Parts

| Part | Quantity | Image |
| --- | --- | ---|
| `Dynamixel XL430-W250-T (ID 1, 2 3, 4, 5 and 6)` | 6 | Dynamixel XL430-W250-T |
| `OpenCR` | 1 | OpenCR |
| `Dynamixel Cable` | 1 | Dynamixel Cable |
| `Micro USB Cable` | 1 | |
| `12V Power Supply` | 1 | |
| `Computer` | 1 | |

### Steps

1. Open the [project](../../firmwares/dynamixel_centering/) in PlatformIO.
2. Connect the `Dynamixel control PCB` to the computer with the `micro USB cable`.
3. Connect the `Dynamixel control PCB` and a `Dynamixel XL430-W250-T` with the `Dynamixel cable`.
4. Connect the `12V power supply` to the `Dynamixel control PCB`.
5. Change the value of `MOTOR_ID` according to the current `Dynamixel XL430-W250-T.
6. Program the `Dynamixel control PCB`.
7. Open the serial monitor.
8. Wait until the `Dynamixel XL430-W250-T` is centered.
9. Repeat steps 3 to 8 for each `Dynamixel XL430-W250-T`.

## B. Dynamixel Pre-Assembly

### Required Parts

| Part | Quantity | Image |
| --- | --- | --- |
| `Dynamixel XL430-W250-T (ID 1, 2, 3, 4 and 5)` | 6 | Dynamixel XL430-W250-T |
| `Stewart Horn Left M2.5` | 2 | Stewart Horn Left M2.5 |
| `Stewart Horn Left M3` | 2 | Stewart Horn Left M3 |
| `Stewart Horn Right M2.5` | 2 | Stewart Horn Right M2.5 |
| `Stewart Horn Right M3` | 2 | Stewart Horn Right M3 |
| `M2x12mm Socket Screw` | 24 | M2x12mm Socket Screw |

### Steps

1. Install a `stewart horn left M2.5` onto each `Dynamixel XL430-W250-T with the ID 2 and 6` with the `M2x12mm socket screws`, as shown in
   the following picture.

Stewart Horn Left M2.5

2. Install the `stewart horn left M3` onto the `Dynamixel XL430-W250-T with the ID 4` with the `M2x12mm socket screws`, as shown in
   the following picture.

Stewart Horn Left M3

3. Install a `stewart horn right M2.5` onto each `Dynamixel XL430-W250-T with the ID 1 and 5` with the `M2x12mm socket screws`, as shown in
   the following picture.

Stewart Horn Right M2.5

4. Install the `stewart horn right M3` onto the `Dynamixel XL430-W250-T with the ID 3` with the `M2x12mm socket screws`, as shown in
   the following picture.

Stewart Horn Right M3

## C. Stewart Platform Rod Pre-Assembly

### Required Parts

| Part | Quantity | Image |
| --- | --- | --- |
| `Ball Joint - M3xL20mm Silver` | 12 | Ball joint - M3xL26mm Silver |
| `Threaded Rod - M3x170mm` | 6 | Threaded Rod - M3x180mm |

### Steps

1. Apply threadlocker to the ends of a `threaded rod`.
2. Screw a ball joint to each ends of the `threaded rod` until the distance between the centers of the ball joint holes
   is 191 mm.
3. Repeat steps 1 to 2 for each `threaded rod`.

Threaded Rod

## D. Stewart Platform

### Required Parts

| Part | Quantity | Image |
| --- | --- | --- |
| `Stewart Bottom 1` | 1 | Stewart Bottom 1 |
| `Stewart Bottom 2` | 1 | Stewart Bottom 2 |
| `Stewart Bottom 3` | 1 | Stewart Bottom 3 |
| `Stewart Top` | 1 | Stewart Top |
| `USB Hub Stand` | 4 | USB Hub Support |
| `Assembled Dynamixel XL430-W250-T (ID 1, 2 3, 4, 5 and 6)` | 6 | Stewart Horn Left M2.5 Stewart Horn Left M3 Stewart Horn Right M2.5 Stewart Horn Right M3 |
| `Dynamixel Cable` | 7 | Dynamixel Cable |
| `Dynamixel XL430-W250-T Cable Cover` | 6 | Dynamixel XL430-W250-T Cable Cover |
| `Dynamixel Control PCB` | 1 | Dynamixel Control PCB |
| `Assembled Stewart Platform Rod` | 6 | Threaded Rod |
| `USB Hub` | 2 | USB Hub |
| `M3x6 Plastic Screw` | 6 | M3x6 Plastic Screw |
| `M2.5x8 Plastic Screw` | 46 | M2.5x8 Plastic Screw |
| `M2.5x12 Plastic Screw` | 4 | M2.5x12 Plastic Screw |
| `M3x8 Plastic Screw` | 4 | M3x8 Plastic Screw |
| `M3x12 Plastic Screw` | 14 | M3x12 Plastic Screw |
| `Big Spring` | 2 | Big Spring |
| `Small Spring` | 4 | Small Spring |

### Steps

1. Install the `Stewart bottom` parts together with the `M3x6 plastic screws`, as shown in the first following picture. Sand the part if needed.

Stewart Bottom

2. Place the `Assembled Dynamixel XL430-W250-T with the ID 1` under the `Stewart bottom`, according to the following
   picture.

Dynamixel IDS

3. Install the `Assembled Dynamixel XL430-W250-T with the ID 1` with `M2.5x8 plastic screws`.

Dynamixel Screws
Dynamixel Screws
Dynamixel Screws

4. Repeat steps 2 to 3 for the other `Assembled Dynamixel XL430-W250-T`.

5. Install a `M3x8 plastic screw` into the horn of the `Assembled Dynamixel XL430-W250-T with the ID 3`, as as shown in the following picture.

Spring Screw

6. Install a  `M3x12 plastic screw` into the Stewart Bottom near the `Assembled Dynamixel XL430-W250-T with the ID 3`, as as shown in the following picture.

Spring Screw

7. Install a `big spring` as as shown in the following picture.

Spring Screw

8. Repeat steps 5 to 7 for the`Assembled Dynamixel XL430-W250-T with the ID 4`.

9. Install a `M2.5x8 plastic screw` and a `small spring` into the horn of the `Assembled Dynamixel XL430-W250-T with the ID 5`, as as shown in the following picture.

Spring Screw

10. Install a `M2.5x12 plastic screw` and the `small spring` into the Stewart Bottom near the `Assembled Dynamixel XL430-W250-T with the ID 5`, as as shown in the following picture.

Spring Screw

11. Repeat steps 9 to 10 for the`Assembled Dynamixel XL430-W250-T with the ID 1, 2 and 6`.

12. Connect the `Dynamixel with the ID 3` and the `Dynamixel with the ID 4` together with a `Dynamixel cable`.
13. Connect the `Dynamixel with the ID 4` and the `Dynamixel with the ID 5` together with a `Dynamixel cable`.
14. Connect the `Dynamixel with the ID 2` and the `Dynamixel with the ID 1` together with a `Dynamixel cable`.
15. Connect the `Dynamixel with the ID 1` and the `Dynamixel with the ID 6` together with a `Dynamixel cable`.
16. Connect a `Dynamixel cable` into the `Dynamixel with the ID 5`.
17. Connect a `Dynamixel cable` into the `Dynamixel with the ID 6`.
18. Connect a `Dynamixel cable` into the `Dynamixel with the ID 3`.
19. Install the `Dynamixel XL430-W250-T cable covers` onto all `Dynamixel`.
20. Install the `USB hub stands` with `M3x12 plastic screws`, as shown in the following picture.

USB Hub Stands

21. Connect the `Dynamixel cable` of the `Dynamixel with the ID 5` to the `Dynamixel Control PCB`.
22. Connect the `Dynamixel cable` of the `Dynamixel with the ID 6` to the `Dynamixel Control PCB`.
23. Install the `Dynamixel Control PCB` with `M3x8 plastic screws`, as shown in the following picture.

Dynamixel Control PCB Scews

24. Install tie wraps to hold the cables, as shown in the following picture.

Dynamixel Tie Wrap

25. Install an `assembled Stewart platform rod` onto each `Stewart horn` with a `M3x12 plastic screw`, as shown in the
    following picture.

Bottom Rod

26. Align the top `ball joints` with the nearest red line, as shown in the following picture.

Ball Joint

27. Install the `Stewart top` onto the top `ball joints` with `M3x12 plastic screws`, as shown in the following
    pictures.

Stewart Top
Stewart Top

28. Install the `USB hubs` with tie wraps, as shown in the following picture.

USB Hubs

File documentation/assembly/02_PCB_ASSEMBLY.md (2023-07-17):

# 2. PCB Assembly

## A. Adafruit MAX

### Required Parts

| Part | Quantity | Image |
| --- | --- | ---|
| `Adafruit MAX9744 kit` | 2 | Adafruit MAX9744 Kit |

### Steps

1. Solder the two `Adafruit MAX9744 kits` for digital control, but do not solder the
   headers ([instructions](https://learn.adafruit.com/adafruit-20w-stereo-audio-amplifier-class-d-max9744/assembly)).

Soldered Adafruit MAX9744

2. Solder the `AD1` bridge on one of the `Adafruit MAX9744 kit`.

Soldered Adafruit MAX9744

## B. PSU Control PCB

### Required Parts

See the [bill of materials](00_ORDER_PRINT_LASER_CUTTING.md#psu-control-pcb).

### Steps

1. Solder U3.
2. Solder C1.
3. Solder R9 and R10.
4. Solder R40 and R41.
5. Solder R14.
6. Solder R11 and R12.
7. Solder C3.

PSU Control PCB - 1

8. Solder Q2.
9. Solder Q3.
10. Solder R5, R6 and R13.
11. Solder C2.
12. Solder R39.
13. Solder R15, R18, R27, R28, R29, R30, R31, R32, R33, R34, R35 and R36.
14. Solder C7, C11, C12, C13, C15 and C16.

PSU Control PCB - 2

15. Solder TH2.
16. Solder R25 and R26.
17. Solder C25, C26, C27, C28, C29 and C30.

PSU Control PCB - 3

18. Solder U5.
19. Solder U8.
20. Solder C14 and C22.
21. Solder R3 and R4.
22. Solder R37 and R38.

PSU Control PCB - 4

23. Solder U7.
24. Solder C17, C18, C19, C20 and C21.

PSU Control PCB - 5

25. Solder Q4.
26. Solder R23 and R24.
27. Solder R21 and R22.
28. Solder D1, D2 and D3.
29. Solder C10 and C24.
30. Solder D6.
31. Solder U6.
32. Solder C8.
33. Solder R42.

PSU Control PCB - 6

34. Solder R43 and R44.
35. Solder C4 and C31.

PSU Control PCB - 7

36. Solder all JST PH male connectors (SW1, SW2, Sw3, SW4, SW5, SW6, J7, J8, J11, J12, J13, J14, J15, D4, D5, M1 and  M2).
36. Solder all JST XH male connectors (J6).
37. Solder L1 and L2.
38. Solder LS1.
39. Solder the fuse holders (F1).
40. Clip the fuse (F1).
41. Solder C5, C9 and C23.
42. Solder J1, J2 and J4.
43. Solder U4.
44. Cut the trace between the pads to separate VIN from VUSB.

Teensy

45. Solder the male headers to the Teensy LC.

Teensy

46. Solder the female headers (U2) to the PCB.
47. Solder D7.
48. Solder C6.
49. Clip the Teensy LC onto the PCB.

PSU Control PCB - 8

## C. 12V Buck-Boost PCB

### Required Parts

See the [bill of materials](00_ORDER_PRINT_LASER_CUTTING.md#buck-boost-pcb).

### Steps

1. Solder U2.
2. Solder D2 and D3.
3. Solder C12 and C16.
4. Solder Q2, Q3, Q4 and Q5.
5. Solder R3.
6. Solder C9, C18 and C24.
7. Solder C10, C13, C14 and C17.
8. Solder R1, R2, R4 and R5.
9. Solder R6, R8 and R10.
10. Solder R11 and D5.
11. Solder C5, C6, C7 and C8.
12. Solder C20, C21, C22 and C23.
13. Solder R7 and R9.
14. Solder U1.
15. Solder C4.
16. Solder Q1.

12V Buck-Boost PCB - SMT

17. Solder R12.
18. Solder L2.
19. Solder J1, J2, J3, J4 and J5.
20. Solder L1.
21. Solder RV2.
22. Solder C1, C2, C3, C11 and C25.
23. Solder RV1.
24. Solder C19.

12V Buck-Boost PCB - All

24. Adjust the output voltage to 11.5 V with RV2.

## D. 19V Buck-Boost PCB

### Required Parts

See the [bill of materials](00_ORDER_PRINT_LASER_CUTTING.md#buck-boost-pcb).

### Steps

1. Solder U2.
2. Solder D2 and D3.
3. Solder C12 and C16.
4. Solder Q2, Q3, Q4 and Q5.
5. Solder R3.
6. Solder C9, C18 and C24.
7. Solder C10, C13, C14 and C17.
8. Solder R1, R2, R4 and R5.
9. Solder R6, R8 and R10.
10. Solder R11 and D5.
11. Solder C5, C6, C7 and C8.
12. Solder C20, C21, C22 and C23.
13. Solder R7 and R9.
14. Solder JP1.

19V Buck-Boost PCB - SMT

15. Solder R12.
16. Solder L2.
17. Solder J1, J2, J3, J4 and J5.
18. Solder L1.
19. Solder RV2.
20. Solder C1, C2, C3, C11 and C25.
21. Solder C19.

19V Buck-Boost PCB - All

21. Adjust the output voltage to 19 V with RV2.

## E. Dynamixel Control PCB

### Required Parts

See the [bill of materials](00_ORDER_PRINT_LASER_CUTTING.md#dynamixel-control-pcb).

### Steps

1. Solder U6.
2. Solder C12.
3. Solder C13.
4. Solder C6.
5. Solder R10.
6. Solder R7 and R8.

PSU Control PCB - 1

7. Solder U5.
8. Solder C7, C8, C9, C10 and C11.

PSU Control PCB - 2

9. Solder U7.
10. Solder U8.
11. Solder R2 and R12.
12. SOlder R14.
13. Solder C15 and C18.

PSU Control PCB - 3

14. Solder Q2.
15. Solder Q3.
16. Solder C25.
17. Solder R15, R16 and R18.
18. Sodler R17.

PSU Control PCB - 4

19. Solder U2.
20. Solder R1 and R3.
21. Solder C4 and C5.

PSU Control PCB - 5

22. Solder C19, C22 and C23.
23. Solder L1 and L2.
24. Solder C1, C3 and C14.
25. Solder C2.
26. Solder R4 and R11.

PSU Control PCB - 6

27. Solder J2.
28. Solder Solder J8, J11 and J12.
29. Solder SW1.
30. Solder U1.
31. Cut the trace between the pads to separate VIN from VUSB.

Teensy

31. Solder the male headers to the Teensy 4.0.

Teensy

32. Solder the female headers (U4) to the PCB.
33. Solder J1.
34. Clip the Teensy 4.0 onto the PCB.

PSU Control PCB - 7

## F. Battery Charger - RRC-PMM240

### Required Parts

| Part | Quantity | Image |
| --- | --- | --- |
| `Battery Charger - RRC-PMM240` | 1 | Battery Charger - RRC-PMM240 |
| `JST B2P-VH Connector` | 2 | JST B2P-VH Connector |

### Steps

1. Desolder the following connectors.

Battery Charger - Desolder

2. Solder the `JST B2P-VH connectors`, as shown in the following picture.

Battery Charger - Desolder

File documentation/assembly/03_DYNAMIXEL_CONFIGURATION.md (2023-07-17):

# 3. Dynamixel Configuration

## Required Parts

| Part | Quantity | Image |
| --- | --- | --- |
| `Dynamixel XL430-W250-T` | 7 | Dynamixel XL430-W250-T |
| `Dynamixel Control PCB`  | 1 | Dynamixel Control PCB |
| `Dynamixel Cable` | 1 | Dynamixel Cable |
| `Micro USB Cable` | 1 | |
| `12V Power Supply` | 1 | |
| `Computer` | 1 | |

## A. Computer Setup
1. Install [Visual Studio Code](https://code.visualstudio.com/download).
2. Install the [PlatformIO extension](https://platformio.org/platformio-ide).

## B. Setup the Dynamixel

1. Open the [project](../../firmwares/dynamixel_setup/) in PlatformIO.
2. Connect the `Dynamixel control PCB` to the computer with the `micro USB cable`.
3. Connect the `Dynamixel control PCB` and a `Dynamixel XL430-W250-T` with the `Dynamixel cable`.
4. Connect the `12V power supply` to the `Dynamixel control PCB`.
5. Change the value of `MOTOR_ID` according to the initial configuration.
6. Change the value of `MOTOR_BAUD_RATE` according to the initial configuration.
7. Change the value of `NEW_MOTOR_ID` to the desired id.
8. Program the `Dynamixel control PCB`.
9. Open the serial monitor.
10. Wait until the baud rate has changed.
11. Disconnect the `12V power supply`.
12. Disconnect the `Dynamixel XL430-W250-T`.
13. Repeat steps 3 to 12 for each `Dynamixel XL430-W250-T`.

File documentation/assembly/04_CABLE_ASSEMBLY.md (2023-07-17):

# 4. Cable Assembly

## A. 16SoundsUSB Cables

### Required Parts

| Part | Quantity | Image |
| --- | --- | ---|
| `RJ12 Connector` | 32 | RJ12 Connector |
| `RJ12 Flat Cable Spool` | 1 | `RJ12 Flat Cable |

### Steps

1. Cut 16 `RJ12 flat cables` of 10 cm long.
2. For each cable, crimp 2 `RJ12 connectors` to create a crossover cable.

Crossover RJ12 Flat Cable

## B.1 LEDs

### Required Parts

| Part | Quantity | Image |
|---| --- |---|
| `White LED` | 2 | White LED |
| `2-Position Female JST PH Connector` | 6 | 2-Position Female JST PH Connector |
| `JST PH Crimp Contact` | 12 | JST PH Crimp Contact |
| `22 AWG Red Wire Spool` | 1 | 22 AWG Red Cable Spool |
| `22 AWG Black Wire Spool` | 1 | 22 AWG Red Cable Spool |
| `Heat Shrink Tube` | 6 | Heat Shrink Tube |

### Steps

1. Cut 2 `22 AWG red wire` of 10 cm long.
2. Cut 2 `22 AWG black wire` of 10 cm long.
3. For each LED, solder a `22 AWG red wire` to the base of the longest LED pin.
4. For each LED, solder a `22 AWG black wire` to the base of the other LED pin.
5. Cut each LED pin at the base.

Soldered LEDs

6. Crimp a `JST PH crimp contact` onto each wire.

LED Crimp Contacts

7. For each white LED, twist the wires.

LED Twisted Wire

8. Add a `heat shrink tube` onto the pins of each LED.

LED Heat Shrink Tube

9. For each LED, insert the crimp contacts into a `2-position female JST PH connector`, as shown in the following
   picture.

LED JST XH

## B.2 RGB LEDS

### Required Parts

| Part | Quantity | Image |
|---| --- |---|
| `LED Strip 30 per m` | 1 | LED Strip 30 per m |
| `LED Strip 144 per m` | 1 | LED Strip 144 per m |
| `3 Position Female JST XH Cable` | 3 | 3 Position Female JST XH Cable |
| `3 Position Male JST XH Cable` | 2 | 3 Position Male JST XH Cable |

### Steps

1. Cut 2 stripes of 5 leds each using `LED Strip 144 per m`
2. Cut 1 stripe of 28 leds using `LED Strip 30 per m`
3. Cut 1 17cm `3 Position Female JST XH Cable`
4. Cut 1 6cm `3 Position Female JST XH Cable`
5. Cut 1 3cm `3 Position Female JST XH Cable`
6. Cut 1 6cm `3 Position Male JST XH Cable`
7. Cut 1 3cm `3 Position Male JST XH Cable`

8. Solder first 5 leds stripe with 17 cm `3 Position Female JST XH Cable` and 6 cm `3 Position Male JST XH Cable` as shown in the following picture.

LED Strip Long - 5 LEDs

9. Solder second 5 leds stripe with 6 cm `3 Position Female JST XH Cable` and 3 cm `3 Position Male JST XH Cable` as shown in the following picture.

LED Strip Short - 5 LEDs

10. Solder long 28 leds stripe `LED Strip 30 per m` with 3 cm `3 Position Female JST XH Cable` as shown in the following picture.

LED Strip - 28 LEDs

## C. Fans

### Required Parts

| Part | Quantity | Image |
|---| --- | --- |
| `Fan` | 2 | Fan |
| `2-Position Female JST PH Connector`  | 2 | 2-Position Female JST PH Connector |
| `JST PH Crimp Contact` | 4 | JST PH Crimp Contact |
| `Heat Shrink Tube` | 2 | Heat Shrink Tube |

### Steps

1. Remove the cable sleeve from each fan.

Fan Without Sleeve

2. For each fan, cut the wires to 15 cm long.
3. For each fan, cut the yellow wire 3 cm shorter.

Fan Yellow Wire

4. For each fan, twist the wires.
5. For each fan, add a `heat shrink tube` to hold the yellow wire, as shown in the following picture.

Fan Heat Shrink Tube

6. For each fan, crimp a `JST PH crimp contact` onto the red and black wires.

Fan Crimp

7. For each fan, insert the crimp contacts into a `2-position female JST PH connector`, as shown in the following
   picture.

Fan Crimp

## D. Speakers

### Required Parts

| Part | Quantity | Image |
| --- | --- | --- |
| `Speaker (Dayton Audio DMA45-8 1)` | 4 | Fan |
| `20 AWG Red Wire Spool` | 1 | 20 AWG Red Cable Spool |
| `20 AWG Black Wire Spool` | 1 | 20 AWG Red Cable Spool |
| `20 AWG Ferrule` | 8 | 20 AWG Ferrule |
| `20 AWG 0.110" Blade Connector` | 4 | 20 AWG 0.110" Blade Connector |
| `20 AWG 0.250" Blade Connector` | 4 | 20 AWG 0.250" Blade Connector |

### Steps

1. Cut a `20 AWG red wire` of 15 cm long and a `20 AWG black wire` of 15 cm long.
2. Cut a `20 AWG red wire` of 20 cm long and a `20 AWG black wire` of 20 cm long.
3. Cut a `20 AWG red wire` of 35 cm long and a `20 AWG black wire` of 35 cm long.
4. Cut a `20 AWG red wire` of 42 cm long and a `20 AWG black wire` of 42 cm long.
5. For each pair, crimp a `20 AWG 0.250" blade connector` on one end of the black wire.
6. For each pair, crimp a `20 AWG 0.110" blade connector` on one end of the red wire.

7. For each wire, crimp a `20 AWG ferrule` on the other end.

Speaker Twist Heat Shrink Tube

8. Install the wires onto the speakers.

## E. Power Switch

### Required Parts

| Part | Quantity | Image |
|---|---|---|
| `Power Switch` | 1 | Power Switch |
| `22 AWG White Wire Spool` | 1 | 22 AWG White Cable Spool |
| `22 AWG Yellow Wire Spool` | 1 | 22 AWG Yellow Cable Spool |
| `4-Position Female JST PH Connector`  | 1 | 4-Position Female JST PH Connector |
| `JST PH Crimp Contact` | 4 | JST PH Crimp Contact |
| `Heat Shrink Tube` | 4 | Heat Shrink Tube |

### Steps

1. Cut 2 `22 AWG white wire` of 38 cm long.
2. Cut 2 `22 AWG yellow wire` of 38 cm long.
2. Solder the wires to the `power switch`, as shown in the following picture.

Power Switch Wires

3. Add a `heat shrink tube` to protect each tab.
4. Twist the wires.
7. Crimp a `JST PH crimp contact` onto the wires.

Power Switch Crimp

8. Insert the crimp contacts into a `4-position female JST 4PH connector`, as shown in the following picture.

Power Switch JST PH

## F. Limit Switch

### Required Parts

| Part | Quantity | Image |
| --- | --- | --- |
| `Limit Switch` | 1 | Power Switch |
| `22 AWG White Wire Spool` | 1 | 22 AWG White Cable Spool |
| `2-Position Female JST PH Connector` | 2 | 2-Position Female JST PH Connector |
| `JST PH Crimp Contact` | 4 | JST PH Crimp Contact |

### Steps

1. Cut two `22 AWG white wire` of 25 cm long.
2. Solder the wires to the limit switch tabs (C and NC).

Limit Switch Tabs

3. Insert a `heat shrink tube` over each wire.
4. Put the `heat shrink tubes` over the tabs.

Limit Switch Heat Skrink Tubes

5. Crimp a `JST PH crimp contact` onto each wire.

Limit Switch Crimps

6. Twist wire together.

7. Insert the crimp contacts into a `2-position female JST PH connector`, as shown in the following
   picture.

Limit Switch Connector

## G. Adafruit MAX9744

### Required Parts

| Part | Quantity | Image |
| --- | --- | --- |
| `Adafruit MAX9744` | 2 | Adafruit MAX9744 |
| `22 AWG Yellow Wire Spool` | 1 | 22 AWG Brown Cable Spool |
| `22 AWG Green Wire Spool` | 1 | 22 AWG Green Cable Spool |
| `22 AWG Black Wire Spool` | 1 | 22 AWG Black Cable Spool |
| `3-Position Female JST PH Connector` | 2 | 3-Position Female JST PH Connector |
| `JST PH Crimp Contact` | 6 | JST PH Crimp Contact |
| `20 AWG Red Wire Spool` | 1 | 20 AWG Red Cable Spool |
| `20 AWG Black Wire Spool` | 1 | 20 AWG Red Cable Spool |
| `20 AWG Ferrule` | 8 | 20 AWG Ferrule |
| `Heat Shrink Tube` | 2 | Heat Shrink Tube |

### Steps

1. Cut 2 `22 AWG yellow wires` of 55 cm long.
2. Cut 2 `22 AWG green wires` of 55 cm long.
3. Cut 2 `22 AWG black wires` of 55 cm long.
4. For each `Adafruit MAX9744`, solder a yellow wire to the SDA pad.
5. For each `Adafruit MAX9744`, solder a green wire to the SCL pad.
6. For each `Adafruit MAX9744`, solder a black wire to the GND pad.

Adafruit MAX9744 Wires

7. For each `Adafruit MAX9744`, twist the soldered wires.

Adafruit MAX9744 Twisted Wires

8. For each `Adafruit MAX9744`, add a `heat shrink tube` to hold the twisted wires, as shown in the following picture.

Adafruit MAX9744 Heat Shrink Tube

9. For each `Adafruit MAX9744`, crimp a `JST PH crimp contact` onto each wire.

Adafruit MAX9744 Crimp Contacts

10. For each `Adafruit MAX9744`, insert the crimp contacts into a `3-position female JST PH connector`, as shown in the
    following picture.

Adafruit MAX9744 JST PH

11. Cut 2 `20 AWG red wires` of 25 cm long.
12. Cut 2 `20 AWG black wires` of 25 cm long.
13. For each wire, crimp a `20 AWG ferrule` on both ends.

Power Wires

## H. 19V Power Adapter

### Required Parts

| Part | Quantity | Image |
| --- | --- | --- |
| `Robot Power Connector - Male` | 1 | Robot Power Connector - Male |
| `19V Power Adapter` | 1 | |

### Steps

1. Cut the `19V power adapter` cable as shown in the following picture.

Adafruit MAX9744 Heat Shrink Tube

2. Solder the `Robot Power Connector - Male` to the `19V power adapter` cable.
    - Make sure the ground is outside.

## I. Battery Charger

| Part | Quantity | Image |
| --- | --- | --- |
| `Robot Power Connector - Female` | 1 | Robot Power Connector - Female |
| `16 AWG Red Wire Spool` | 1 | 16 AWG Red Cable Spool |
| `16 AWG Black Wire Spool` | 1 | 16 AWG Black Cable Spool |
| `16 AWG Ferrule` | 4 | 16 AWG Ferrule |
| `JST VHR-2N Connector` | 2 | JST VHR-2N Connector |
| `JST SVH-21T-1.1 Crimp Contact` | 4 | JST SVH-21T-1.1 Crimp Contact |
| `JST PHR-6 Cable` | 1 | JST PHR-6 Cable |
| `5-Position Female JST PH Connector` | 1 | 5-Position Female JST PH Connector |
| `JST PH Crimp Contact` | 5 | JST PH Crimp Contact |
| `Heat Shrink Tube` | 2 | Heat Shrink Tube |

### Steps

1. Cut a `16 AWG red wire` of 8 cm long.
2. Cut a `16 AWG black wire` of 8 cm long.
3. For each wire, crimp a `16 AWG ferrule` on one end.

Ferrules

4. For each wire, crimp a `JST SVH-21T-1.1 crimp contact` on the other end.

JST SVH-21T-1.1 crimp contact

5. Insert the wires into a `JST VHR-2N connector`, as shown in the following picture.

JST VHR-2N Connector

6. Cut a `16 AWG red wire` of 30 cm long.
7. Cut a `16 AWG black wire` of 30 cm long.
8. Solder the wires onto the `robot power connector`, as shown in the following picture.

Robot Power Connector - Female

9. Install a `heat shrink tube` onto each wire, as shown in the following picture.

Robot Power Connector - Female - Heat Shrink Tube

10. For each wire, crimp a `JST SVH-21T-1.1 crimp contact` on the other end.

JST SVH-21T-1.1 crimp contact

11. Insert the wires into a `JST VHR-2N connector`, as shown in the following picture.

JST VHR-2N Connector

12. Remove the following wire from the `JST PHR-6 cable`.

JST PHR-6 Cable

13. Cut the `JST PHR-6 cable` wires to 16 cm.
14. For each wire of the `JST PHR-6 cable`, crimp a `JST PH crimp contact`.

JST PHR-6 Cable Crimp

15. Insert the wires into a `5-Position female JST PH connector`, as shown in the following pictures.

JST PHR-6 Connector

## J. Slip Ring Cables

### Required Parts

| Part | Quantity | Image |
| --- | --- | --- |
| `Computer Power Connector` | 1 | Computer Power Connector - Male |
| `T-Connector` | 1 | T-Connector |
| `Male Power Connector` | 2 | Power Connector - Male |
| `Female Power Connector` | 2 | Power Connector - Female |
| `Heat Shrink Tube` | 4 | Heat Shrink Tube |
| `18 AWG Ferrule` | 4 | 18 AWG Ferrule |

### Steps

1. Crimp a `18 AWG ferrule` onto each wire of the first `male power connector` and the first `female power connector`.

Computer Power Connector

2. Insert a `heat shrink tube` onto each remaining `power connector` wire.
2. Solder the black wire of the second `female power connector` to the wire connected to the outside of
   the `computer power connector`.
3. Solder the red wire of the second `female power connector` to the other wire of the `computer power connector`.
4. Install the `heat shrink tubes`.

Computer Power Connector

5. Solder the black wire of the second `male power connector` to the black wire of the `T-connector`.
6. Solder the red wire of the second `male power connector` to the red wire of the `T-connector`.
7. Install the `heat shrink tubes`.

Dynamixel Control Power Connector

## K. Slip Ring

### Required Parts

| Part | Quantity | Image |
| --- | --- | --- |
| `Slip Ring - M220-24 36wire 2A flange A` | 1 | Slip ring |
| `Male Power Connector` | 2 | Power Connector - Male |
| `Female Power Connector` | 2 | Power Connector - Female |
| `3-Position Female JST PH Connector` | 2 | 3-Position Female JST PH Connector |
| `JST PH Crimp Contact` | 6 | JST PH Crimp Contact |
| `Mini-USB Cable` | 1 | Mini-USB Cable |
| `Ethernet Cable` | 1 | Ethernet Cable |
| `Big Heat Shrink Tube` | 14 | Heat Shrink Tube |
| `Small Heat Shrink Tube` | 24 | Heat Shrink Tube |

### Slip Ring Wire Table
Solder the wires according to the following table.

| Usage | Wires |
| --- | --- |
| 12V+ | 1-BLK, 1-BRN, 1-RED, 1-ORG, 1-YEL, 1-GRN, 1-BLU |
| 12V- | 1-PUR, 1-GRY, 1-WHT, 1-PINK, 1-LGT-BLU, 1-WHT-BLK, 2-LGT-BLU |
| 19V+ | 1-WHT-BRN, 1-WHT-RED, 1-WHT-ORG, 1-WHT-YEL, 1-WHT-GRN |
| 19V- | 1-WHT-BLU, 1-WHT-PUR, 1-WHT-GRY, 1-BLK-RED, 1-BLK-BRN, 1-TRANS |
| USB 5V | 2-BRN |
| USB GND | 2-BLK |
| USB Data + | 2-RED |
| USB Data - | 2-ORG |
| Eth TX + | 2-YEL |
| Eth TX - | 2-GRN |
| Eth RX + | 2-BLU |
| Eth RX - | 2-PUR |

### Steps
The following steps are examples.

1. Insert a `big heat shrink tube` onto each `power connector` wire.
2. Solder the black wire of the first `male power connector` to 7 wires of the bottom side of the `slip ring`.
3. Solder the black wire of the first `female power connector` to matching wires of the top side of the `slip ring`.
5. Solder the red wire of the first `male power connector` to 7 wires of the bottom side of the `slip ring`.
6. Solder the red wire of the first `female power connector` to matching wires of the top side of the `slip ring`.
7. Install the `big heat shrink tubes`.

Male Power Connector
Female Power Connector

8. Solder the black wire of the first `female power connector` to 6 wires of the bottom side of the `slip ring`.
9. Solder the black wire of the first `male power connector` to matching wires of the top side of the `slip ring`.
8. Solder the red wire of the first `female power connector` to 5 wires of the bottom side of the `slip ring`.
9. Solder the red wire of the first `male power connector` to matching wires of the top side of the `slip ring`.
10. Install the `big heat shrink tubes`.

Male Power Connector
Female Power Connector

11. Crimp `JST XH crimp contacts` onto 3 wires of the bottom side of the `slip ring`.
12. Crimp `JST XH crimp contacts` onto the matching wire of the top side of the `slip ring`.
13. Insert the crimp contacts into two `3-position female JST PH connectors`, as shown in the following pictures.

Slip Ring JST PH connectors

20. Cut the `Mini-USB cable` in half.
21. Cut 4 wires of the bottom side of the `slip ring` near it.
22. Insert a `small heat shrink tube` onto each wire.
23. Insert a `big heat shrink tube` onto the `Mini-USB cable part`.
24. Solder each wire of the `Mini-USB cable part` onto a cutted wire.
25. Install the `small heat shrink tubes`.
26. Install the `big heat shrink tube`.

Mini-USB

27. Cut the matching wires of the top side of the `slip ring` near it.
28. Insert a `small heat shrink tube` onto each wire.
29. Insert a `big heat shrink tube` onto the `USB-A cable part`.
30. Solder each wire of the `USB-A cable part` onto the matching cutted wire.
31. Install the `small heat shrink tubes`.
32. Install the `big heat shrink tube`.

USB-A

33. Cut the `Ethernet cable` in half.
34. Cut 4 wires of the bottom side of the `slip ring` near it.
35. Insert a `small heat shrink tube` onto each wire.
36. Insert a `big heat shrink tube` onto a `Ethernet cable part`.
37. Solder the TX wires and the RX wires of the `Ethernet cable part` onto the cutted wires.
38. Install the `small heat shrink tubes`.
39. Install the `big heat shrink tube`.
40. Cut the matching wires of the top side of the `slip ring` near it.
41. Insert a `small heat shrink tube` onto each wire.
42. Insert a `big heat shrink tube` onto a `Ethernet cable part`.
43. Solder the TX wires and the RX wires of the `Ethernet cable part` onto the matching cutted wires.
44. Install the `small heat shrink tubes`.
45. Install the `big heat shrink tube`.

Ethernet

## L. Buck-Boost Wires

### Required Parts

| Part | Quantity | Image |
| --- | --- | --- |
| `16 AWG Red Wire Spool` | 1 | 16 AWG Red Cable Spool |
| `16 AWG Black Wire Spool` | 1 | 16 AWG Black Cable Spool |
| `16 AWG Ferrule` | 8 | 16 AWG Ferrule |

### Steps

1. Cut a `16 AWG red wire` of 14 cm long.
2. Cut a `16 AWG black wire` of 14 cm long.
3. Cut a `16 AWG red wire` of 16 cm long.
4. Cut a `16 AWG black wire` of 16 cm long.
5. For each wire, crimp a `16 AWG ferrule` on both ends.

## M. Light Sensor

### Required Parts
| Part | Quantity | Image |
|---|---|---|
| `Light Sensor` | 4 | Push Button |
| `22 AWG Red Wire Spool` | 1 | 22 Red Cable Spool |
| `22 AWG Black Wire Spool` | 1 | 22 AWG Black Cable Spool |
| `22 AWG White Wire Spool` | 1 | 22 AWG White Cable Spool |
| `3-Position Female JST PH Connector`  | 4 | 3-Position Female JST PH Connector |
| `JST PH Crimp Contact` | 12 | JST PH Crimp Contact |

### Steps
1. Cut a `22 AWG red wire` of 29 cm long.
2. Cut a `22 AWG black wire` of 29 cm long.
3. Cut a `22 AWG white wire` of 29 cm long.
4. Cut a `22 AWG red wire` of 30 cm long.
5. Cut a `22 AWG black wire` of 30 cm long.
6. Cut a `22 AWG white wire` of 30 cm long.
7. Cut a `22 AWG red wire` of 41 cm long.
8. Cut a `22 AWG black wire` of 41 cm long.
9. Cut a `22 AWG white wire` of 41 cm long.
10. Cut a `22 AWG red wire` of 54 cm long.
11. Cut a `22 AWG black wire` of 54 cm long.
12. Cut a `22 AWG white wire` of 54 cm long.
13. Solder the 3 wires of the same dimensions on each of the `light sensor`.

Light Sensors Wires

14. For each `light sensor`, crimp a `JST PH crimp contact` onto each wire.

Light Sensors Wires

15. For each `light sensor`, insert the crimp contacts into a `3-position female JST PH connector`, as shown in the following
   picture.

Light Sensors JST PH connector

## N. Push Buttons

### Required Parts
| Part | Quantity | Image |
|---|---|---|
| `Push Button` | 4 | Push Button |
| `22 AWG White Wire Spool` | 1 | 22 AWG White Cable Spool |
| `Heat Shrink Tube` | 8 | Heat Shrink Tube |
| `2-Position Female JST PH Connector`  | 4 | 2-Position Female JST PH Connector |
| `JST PH Crimp Contact` | 12 | JST PH Crimp Contact |

### Steps
1. Cut 8 `22 AWG white wire` of 9 cm long.
2. For each `push button`, solder 2 wires.

Push Buttons Wires

3. Insert a `heat shrink tube` onto each wire.
4. Install the `heat shrink tubes`, as shown in the following picture.

Push Buttons Heat Shrink Tubes

5. For each `push button`, crimp a `JST PH crimp contact` onto each wire.

Push Buttons Crimps

6. Twist wire together.

7. For each `push button`, insert the crimp contacts into a `2-position female JST PH connector`, as shown in the following
   picture.

Push Buttons

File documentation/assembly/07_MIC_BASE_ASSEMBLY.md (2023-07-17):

# 7. Mic Base Assembly

## A. Microphone Gain Increase

### Required Parts

| Part | Quantity | Image |
| --- | --- | --- |
| `16SoundsUSB` | 1 | 16SoundsUSB |
| `xSoundsMicrophones` | 16 | xSoundsMicrophones |
| `16SoundsUSB Cable` | 16 | 16SoundsUSB Cable |
| `Mini USB Cable` | 1 | |
| `Computer` | 1 | |

### Steps

1. Install Audacity on the computer.
2. Connect all `xSoundsMicrophones` to the `16SoundsUSB` with `16SoundsUSB cables`.
3. Connect the `16SoundsUSB` to the computer with the `mini USB cable`.
4. Open Audacity.
5. Start the recording with the `16SoundsUSB`.
6. For each `xSoundsMicrophones`, turn the potentiometer counterclockwise to increase the gain until the sound level is
   stable.

xSoundsMicrophones

## B. Mic Base Pre-Assembly

### Required Parts

| Part | Quantity | Image |
| --- | --- | --- |
| `Base Mic` | 4 | Base Mic |
| `Magnet` | 16 | Magnet |
| `xSoundsMicrophones` | 16 | xSoundsMicrophones |
| `M3x5mm Plastic Screw` | 64 | M3x5mm Plastic Screw |

### Steps
1. Install four `magnets` with super glue into the dedicated holes on each of the `base mic`, as shown in the following picture.

Mic Base Pre-Assembly 1

2. For each `base mic` part, use `M3x5mm plastic screws` to install 4 `xSoundsMicrophones`, as shown in
   the following picture.

Mic Base Pre-Assembly 2
Mic Base Pre-Assembly 3

## C. Mic Base Assembly

### Required Parts

| Part | Quantity | Image |
| --- | --- | --- |
| `Audio Base Assembly` | 1 | |
| `Mic Base Pre-Assembly`  | 4 | |
| `M3x12mm Plastic Screw`  | 8 | M3x12mm Plastic Screw |

### Steps

1. Install `mic base pre-assemblies` onto the `audio base assembly` with `M3x12mm plastic screws`, as shown in the
   following picture.

Mic Base

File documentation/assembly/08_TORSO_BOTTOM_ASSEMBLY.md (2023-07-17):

# 8. Torso Bottom Assembly

## A. Dynamixel Pre-Assembly

### Required Parts

| Part | Quantity | Image |
| --- | --- | --- |
| `Dynamixel XL430-W250-T (ID7)` | 1 | Dynamixel XL430-W250-T |
| `Torso Bottom Gear` | 1 | Torso Bottom Gear |
| `M2x12mm Socket Screw` | 4 | M2x12mm Socket Screw |

### Steps

1. Install the `torso bottom gear` onto the `Dynamixel XL430-W250-T` with the `M2x12mm socket screws`, as shown in the
   following picture.

Dynamixel Gear

## B. Torso Bottom Holder

### Required Parts

| Part | Quantity | Image |
| --- | --- | --- |
| `Torso Bottom Holder` | 3 | Torso Bottom Holder |
| `605zz` | 3 | 605zz |
| `M5x16 Socket Screw`  | 3 | M5x16 Socket Screw |
| `M5 Washer` | 6 | M5 Washer |

### Steps

1. Place a `M5 washer` on either side of a `605zz` bearing.
2. Install the `605zz` bearing and the `M5 washers` into the `torso bottom holder` with a `M5x16mm socket screw`, as
   shown in the following picture.

Assembled Torso Bottom Holder

2. Repeat steps 1 to 2 for the remaining parts.

## C. Torso Bottom - 3D Printed Parts

### Required Parts

| Part | Quantity | Image |
| --- | --- | --- |
| `Torso Bottom External 1` | 1 | Torso Bottom External 1 |
| `Torso Bottom External 2` | 1 | Torso Bottom External 1 |
| `Torso Bottom External 3` | 1 | Torso Bottom External 1 |
| `Torso Bottom Internal Xavier` or `Torso Bottom Internal Orin` | 1 | Torso Bottom Internal Xavier or Torso Bottom Internal Orin |
| `Base Gear 1` | 1 | Base Gear |
| `Base Gear 2` | 1 | Base Gear |
| `Base Gear 3` | 1 | Base Gear |
| `Base Gear 4` | 1 | Base Gear |
| `Assembled Torso Bottom Holder` | 3 | Assembled Torso Bottom Holder |
| `Limit Switch Bracket` | 1 | Limit Switch Support |
| `Torso Bottom Magnet Bracket` | 1 | Torso Bottom Magnet Bracket |
| `Gear Servo Bracket` | 1 | Gear Servo Support |
| `605zz` | 6 | 605zz |
| `M3x6 Plastic Screw` | 10 | M3x6 Plastic Screw |
| `M5x16 Socket Screw` | 3 | M5x16 Socket Screw |
| `M5x30 Socket Screw` | 3 | M5x30 Socket Screw |
| `M5x16 Washer` | 15 | M5x16 Washer |
| `M3x12 Plastic Screw` | 12 | M3x12 Plastic Screw |

### Steps

1. Install the `torso bottom external` parts together with the `M3x6 plastic screws`, as shown in the first following picture. Sand the part if needed.

Torso Bottom External

2. Install the `base gear` parts together with the `M3x6 plastic screws`, as shown in the first following picture. Sand the part if needed.

Base Gear

3. Install a `magnet` with super glue into the dedicated hole of the `limit switch bracket`, as shown in the following picture.

Limit Switch Bracket Magnet

4. Install a `magnet` with super glue into the dedicated hole of the `torso bottom magnet bracket`, as shown in the following picture.

Torso Bottom Magnet Bracket Magnet

5. Install a `magnet` with super glue into the dedicated hole of the `gear servo bracket`, as shown in the following picture.

Gear Servo Bracket Magnet

6. Place the `assembled torso bottom external` and the `torso bottom internal`, as shown in the first following picture. Make
   sure the small holes in the `assembled torso bottom external` are aligned with the `torso bottom internal`. The holes for
   screws holding the `605zz` bearings must be closer to the bottom (`slip ring` hole), as shown in the second following
   picture.

Torso Bottom Placement
Hole Placement

7. Put 6 `M3x12 plastic screws` to fix the parts together (2 screws per branch).

Torso Bottom Screws

8. Place a `M5 washer` on either side of a `605zz` bearing.
9. Install the `605zz` bearing and the `M5 washers` into a hole between the branches with a `M5x16mm socket screw`, as
   shown in the following picture.

605zz 1

10. Repeat steps 3 to 4 for all holes between the branches.

605zz 2

11. Put a `M5 washer` onto a `M5x30 socket screw`.

M5 Washer

12. Place a `M5 washer` on either side of a `605zz` bearing.
13. Install the `605zz` bearing and the `M5 washers` into a hole aligned with the branches with a `M5x30mm socket screw`,
   as shown in the following picture.

605zz 3

14. Repeat steps 6 to 8 for all holes aligned with the branches.

605zz 4

15. Flip the assembly.
16. Install the `assembled base gear` as shown in the following picture.

Base Gear

17. Install all `assembled torso bottom holders` with `M3x12 plastic screws`.

Torso Bottom Holder 1
Torso Bottom Holder 2

18. Install the `limit switch bracket` with `M3x12 plastic screws`.

Limit Switch Bracket

19. Install the `torso bottom magnet bracket` with `M3x12 plastic screws`.

Torso Bottom Magnet Bracket

20. Install the `gear servo bracket` with `M3x12 plastic screws`.

Gear Servo Bracket

## D. Torso Bottom - Antennas - Jetson AGX Xavier

### Required Parts

| Part | Quantity | Image |
| --- | --- | --- |
| `Stewart Stand` | 2 | Stewart Stand |
| `WiFi Antenna` | 2 | WiFi Antenna |

### Steps

1. Install a `WiFi antenna` to a `Stewart stand`, as shown in the following picture.

Antenna 1

2. Install the other `WiFi antenna` to the other `Stewart stand`, as shown in the following picture.

Antenna 2

## E. Torso Bottom - Electronics - Jetson AGX Xavier

### Required Parts

| Part | Quantity | Image |
| --- | --- | --- |
| `Nvidia Jetson AGX Xavier` | 1 | Nvidia Jetson AGX Xavier |
| `Stewart Stand With An Antenna` | 2 | Antenna 1 |
| `Stewart Stand` | 1 | Stewart Stand |
| `Assembled Torso Bottom Dynamixel` | 1 | Assembled Torso Bottom Dynamixel |
| `Assembled Limit Switch` | 1 | Assembled Limit Switch |
| `M3x55 Socket Screw` | 4 | M3x55 Socket Screw |
| `M3x12 Plastic Screw` | 6 | M3x12 Plastic Screw |
| `M2.5x8 Plastic Screw` | 6 | M2.5x8 Plastic Screw |
| `M2.5x12 Plastic Screw` | 2 | M2.5x12 Plastic Screw |
| `Magnet` | 3 | Magnet |

### Steps

1. Install a `magnet` with super glue into the dedicated hole of each `Stewart stand`, as shown in the following picture.

Stewart Stand Magnet

2. Remove the following screws.

Nvidia Jetson AGX Xavier Screws

3. Install the `Nvidia Jetson AGX Xavier` onto the assembly with `M3x55 socket screws`.

Nvidia Jetson AGX Xavier

4. Install the `assembled torso bottom dynamixel` onto the assembly with `M2.5x8 plastic screws`, as shown in the following pictures.

Dynamixel
Dynamixel

5. Install the `stewart stand` onto the assembly with `M3x12 plastic screws`, as shown in the following pictures.

Stewart Stand
Stewart Stand

6. Install the first `stewart stand with an antenna` onto the assembly with `M3x12 plastic screws`, as shown in the following pictures.

Antenna 1
Stewart Stand

7. Install the second `stewart stand with an antenna` onto the assembly with `M3x12 plastic screws`, as shown in the following pictures.

Antenna 1
Stewart Stand

8. Install the `assembled limit switch` onto the assembly with `M2.5x12 plastic screws`.

Limit Switch

9. Connect the `WiFi antennas` to the `WiFi card`.

WiFi Antennas

## E. Torso Bottom - Electronics - Jetson AGX Orin

### Required Parts

| Part | Quantity | Image |
| --- | --- | --- |
| `Nvidia Jetson AGX Orin` | 1 | Nvidia Jetson AGX Orin |
| `RTC Clock Battery` | 1 | RTC Clock Battery |
| `Stewart Stand` | 3 | Stewart Stand |
| `Assembled Torso Bottom Dynamixel` | 1 | Assembled Torso Bottom Dynamixel |
| `Assembled Limit Switch` | 1 | Assembled Limit Switch |
| `M3x12 Plastic Screw` | 6 | M3x12 Plastic Screw |
| `M2.5x8 Plastic Screw` | 6 | M2.5x8 Plastic Screw |
| `M2.5x12 Plastic Screw` | 2 | M2.5x12 Plastic Screw |
| `Magnet` | 3 | Magnet |

### Steps

1. Install the `RTC clock battery` as shown in the following picture.

RTC Clock Battery

2. Install a `magnet` with super glue into the dedicated hole of each `Stewart stand`, as shown in the following picture.

Stewart Stand Magnet

3. Remove the following screws.

Nvidia Jetson AGX Orin Screws

4. Remove the stand.

5. Install the `Nvidia Jetson AGX Orin` onto the assembly with removed screws, as shown in the following picture.

Nvidia Jetson AGX Orin

6. Install the `assembled torso bottom dynamixel` onto the assembly with `M2.5x8 plastic screws`, as shown in the following pictures.

Dynamixel
Dynamixel

7. Install the `stewart stands` onto the assembly, as shown in the following picture.

Stewart Stand

8. Install the `assembled limit switch` onto the assembly with `M2.5x12 plastic screws`.

Limit Switch

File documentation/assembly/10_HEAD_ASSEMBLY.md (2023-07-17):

# 10. Head Assembly

## A. Parts Pre-Assembly

### Required Parts

| Part | Quantity | Image |
| --- | --- | --- |
| `HDMI Cable` | 1 | HDMI Cable |
| `270-Degree HDMI Adapter` | 1 | 270-Degree HDMI Adapter |
| `Touchscreen` | 1 | Touchscreen |
| `M3x5mm Screw Included with the Touchscreen` | 4 | M3x5mm Screw |
| `Spacer Included with the Touchscreen` | 4 | Spacer |
| `Intel RealSense D435i` | 1 | Intel RealSense D435i |
| `Wide Angle Camera` | 1 | Wide Angle Camera |
| `Wide Angle Camera Lens` | 1 | Wide Angle Camera Lens |

### Steps

1. Connect a `270-degree HDMI adapter` to one end of the `HDMI cable`, as shown in the following picture.

HDMI Cable

2. Install the `spacers` onto the `touchscreen`, as shown in the following pictures.

Touchscreen
Touchscreen

3. Turn on the `touchscreen` as shown in the following picture.

Touchscreen Switch

4. Remove the USB-C protector from the `Intel RealSense D435i`, as shown in the following picture.

Intel RealSense D435i

5. Remove the `lens` of the `wide angle camera`.
6. Install the `wide angle camera lens` onto the `wide angle camera`.
7. Connect the provided USB cable to the `wide angle camera`.
8. Set the focus of the `wide angle camera` to infinity.

## B. Head

### Required Parts

| Part | Quantity | Image |
| --- | --- | --- |
| `Head` | 1 | Head |
| `Head Cable Protector` | 1 | Head Cable Protector |
| `Assembled Touchscreen` | 1 | Touchscreen |
| `Intel RealSense D435i` | 1 | Intel RealSense D435i |
| `HDMI Cable (1.5 ft)` | 1 | HDMI Cable |
| `Micro-USB Cable - Right Angle` | 1 | Micro-USB Cable - Right Angle |
| `USB-C Cable Included with the Intel RealSense D435i` | 1 | |
| `90-Degree USB-C Adapter` | 1 | 90-Degree USB-C Adapter |
| `M3x12 Plastic Screw` | 10 | M3x12 Plastic Screw |
| `M3x10mm Socket Screw` | 6 | M3x10mm Socket Screw |
| `Magnet` | 8 | Magnet |

### Steps

1. Install the `head` onto the `Stewart top` with `M3x12 plastic screws`, as shown in the following pictures.

Head
Head

2. Install the `touchscreen` onto the `head` with `M3x10mm socket screws`, as shown in the following pictures.

Touchscreen
Touchscreen

3. Connect the `HDMI cable` to the `touchscreen`.
4. Connect the `micro-USB cable` to the `touchscreen`, as shown in the following picture.

Touchscreen Cable

5. Install a `magnet` with super glue into the dedicated hole of the `head cable protector`, as shown in the following pictures.

Head Cable Protector Magnets
Head Cable Protector Magnets
Head Cable Protector Magnets
Head Cable Protector Magnets

6. Install the `Intel RealSense D435i` onto the `head` with `M3x10mm socket screws`, as shown in the following picture.

Intel RealSense D435i

7. Install the `wide angle camera` onto the `head` with `M2.5x5 plastic screws`, as shown in the following picture.

Wide Angle Camera

8. Install the `head cable protector` onto the `head` with `M3x12 plastic screws`, as shown in the following pictures.

Head Cable Protector
Head Cable Protector
Head Cable Protector

9. Connect the `90-degree USB-C adapter` to the `Intel RealSense D435i`.
10. Connect the `USB-C cable` to the `90-degree USB-C adapter`.
11. Roll the USB cables to the `Stewart top`, attach them with a tie wrap and connect them to a `USB hub`.

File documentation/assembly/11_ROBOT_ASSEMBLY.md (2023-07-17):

# 11. Robot Assembly

## A. Base/Torso Bottom Assembly

### Required Parts

| Part | Quantity | Image |
| --- | --- | --- |
| `Base Assembly` | 1 | |
| `Assembled Slip Ring` | 1 | |
| `1/8-Inch Stereo Jack Cable` | 2 | |
| `16SoundsUSB` | 1 | 16SoundsUSB |
| `M3x8mm Plastic Screw` | 4 | M3x8mm Plastic Screw |
| `16SoundsUSB Cable` | 16 | 16SoundsUSB Cable |
| `Torso Bottom Assembly` | 1 | |
| `M5x10mm Plastic Screw` | 3 | M5x10mm Plastic Screw |
| `M3x12mm Plastic Screw` | 16 | M3x12mm Plastic Screw |
| `Computer Power Connector` | 1 | Computer Power Connector |
| `Dynamixel Control Power Connector` | 1 | OpenCR Power Connector |

### Steps

1. Connect the bottom `Ethernet connector` of the `assembled slip sing` to the base connector.
2. Connect the bottom `power connectors` of the `assembled slip sing` to `power connectors` connected
   the `Buck-Boost PCBs`.
3. Connect the `JST PH connector` of the `assembled slip sing` to the following connector of the `PSU Control PCB`.

PSU Control RS232

4. Connect the `1/8-Inch stereo jack cables` to the `ground loop noise isolators`.
5. Connect the `1/8-Inch stereo jack cables` to the `16SoundsUSB`.
6. Connect the `Mini-USB cable` to the `16SoundsUSB`.
7. Install the `16SoundsUSB` into the base with `M3x8mm plastic screws`, as shown in the following picture.

16SoundsUSB

8. Install the `assembled slip ring` into the `torso bottom assembly` with `M5x10mm plastic screws`, as shown in the
   following picture.

Slip Ring

9. Connect all `16SoundsUSB cables`.

10. Install the `torso bottom assembly` onto the base with `M3x12mm plastic screws`, as shown in the following picture.

Torso

11. Connect the `computer power connector` to the top `power connector` of the `assembled slip sing`.
12. Connect the `Dynamixel control power connector` to the top `power connector` of the `assembled slip sing`.
13. Connect the `computer power connector` and the the `Ethernet connector` to the `Nvidia Jetson AGX Xavier` or `Nvidia Jetson AGX Orin`.
14. Secure the wires with tie wraps.

## B. Torso Bottom/Stewart Platform Assembly

### Required Parts

| Part | Quantity | Image |
| --- | --- | ---|
| `Torso Bottom Assembly` | 1 | |
| `Stewart Platform Assembly` | 1 | |
| `M3x12mm Plastic Screw` | 6 | M3x12mm Plastic Screw |
| `Micro-USB Cable Included with the Touchscreen` | 1 | Micro-USB Cable |

### Steps

1. Place the `Stewart platform assembly` onto the `torso bottom assembly` without installing the screws, as shown in the
   following picture.

Stewart Platform Assembly

2. Connect the `Dynamixel control power connector` to the `Dynamixel control PCB` (the cable must pass through the `Stewart bottom` hole).
3. Connect the `limit switch connector` to the following connector of the `Dynamixel control PCB` (the cable must pass through the `Stewart bottom` hole).

JST PH

4. Connect the `slip ring JST PH connector` to the following connector of the `Dynamixel control PCB` (the cable must pass through the `Stewart bottom` hole).

JST PH

5. Connect the `Micro-USB cable included with the touchscreen` to the `Dynamixel control PCB` and a `USB hub`.
6. Connect the `USB hubs` to `Nvidia Jetson AGX Xavier` (the cables must pass through the `Stewart bottom` hole).
7. Connect the `HDMI cable` with a `270-Degree HDMI adapter` or with `Display port adapters` to `Nvidia Jetson AGX Xavier` or `Nvidia Jetson AGX Orin` (the cable must pass through the `Stewart bottom` hole).
8. Install the `M3x12mm plastic screws` to fix the `Stewart platform assembly` onto the `torso bottom assembly`.

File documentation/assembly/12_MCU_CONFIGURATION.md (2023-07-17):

# 12. MCU Configuration

## Required Parts

| Part | Quantity |
| --- | --- |
| `Micro USB Cable` | 1 |
| `19V Power Adapter` | 1 |
| `Assembled Robot` | 1 |

## A. Computer Setup
1. Install [Visual Studio Code](https://code.visualstudio.com/download).
2. Install the [PlatformIO extension](https://platformio.org/platformio-ide).

## B. Setup the PSU Control PCB

1. Open the [project](../../firmwares/psu_control) in PlatformIO.
3. Change the value `FIRMWARE_MODE` in [config.h](../../firmwares/psu_control/include/config.h)
   to `FIRMWARE_MODE_NORMAL`.
4. Connect the micro USB cable to the computer and the robot base.
5. Turn off the robot.
6. Connect the `19V Power Adapter` to the base.
7. Turn on the robot.
8. Click on the upload button.

## C. Setup the Dynamixel Control PCB

1. Open the [project](../../firmwares/dynamixel_control) in PlatformIO.
3. Change the value `FIRMWARE_MODE` in [config.h](../../firmwares/psu_control/include/config.h)
   to `FIRMWARE_MODE_NORMAL`.
4. Connect the micro USB cable to the computer and the `Dynamixel Control PCB`.
5. Turn off the robot.
6. Connect the `19V Power Adapter` to the base.
7. Turn on the robot.
8. Click on the upload button.

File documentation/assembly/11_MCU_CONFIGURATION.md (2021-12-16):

# 11. MCU Configuration

## Required Parts
| Part | Quantity |
| --- | --- |
| `Micro USB Cable` | 1 |
| `19V Power Adapter` | 1 |
| `Assembled Robot` | 1 |

## A. Computer Setup
1. Install [Visual Studio Code](https://code.visualstudio.com/download).
2. Install the [PlatformIO extension](https://platformio.org/platformio-ide).
3. Install the Arduino IDE.
    - [Windows](https://www.arduino.cc/en/Guide/Windows)
    - [Linux](https://www.arduino.cc/en/Guide/Linux)
4. Install the [OpenCR Board](https://emanual.robotis.com/docs/en/parts/controller/opencr10/#install-on-linux).

## C. Setup the Teensy LC
1. Open the [project](../../firmwares/psu_control) in PlatformIO.
2. Change the value of `INA_TYPE` in [config.h](../../firmwares/psu_control/include/config.h) to the chip you have soldered (`INA220_TYPE` or `INA226_TYPE`).
3. Change the value `FIRMWARE_MODE` in [config.h](../../firmwares/psu_control/include/config.h) to `FIRMWARE_MODE_NORMAL`.
4. Connect the micro USB cable to the computer and the robot base.
5. Turn off the robot.
6. Connect the `19V Power Adapter` to the base.
7. Turn on the robot.
8. Click on the upload button.

## D. Setup the OpenCR
1. Modify `dynamixel_driver.cpp` (~/.arduino15/packages/OpenCR/hardware/OpenCR/1.4.9/libraries/DynamixelWorkbench/src/dynamixel_workbench_toolbox/dynamixel_driver.cpp).
    1. Comment out the `delay` line in `bool writeRegister(uint8_t, uint16_t, uint16_t, uint8_t*, const char**);`.
    2. Comment out the `delay` line in `bool writeRegister(uint8_t, const char*, int32_t, const char**);`.
    3. Comment out the `delay` line in `bool writeOnlyRegister(uint8_t, uint16_t, uint16_t, uint8_t*, const char**);`.
    4. Comment out the `delay` line in `bool writeOnlyRegister(uint8_t, const char*, int32_t, const char**);`.
2. Open the [project](../../firmwares/opencr_firmware) in the Arduino IDE.
3. Click on the upload button.

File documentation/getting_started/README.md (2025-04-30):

# Getting Started

This is a guide to help you get started with the project. It covers the basic setup, configuration, and usage of the project.
It is recommended to follow the steps in order to ensure a smooth experience. All the steps assume that you are working directly on the robot using the terminal or Visual Studio Code with SSH.

## Prerequisites

- A T-Top robot with Jetson Orin AGX or Xavier AGX with Jetpack 5.x.x
- ROS 2 Humble pre-installed on the robot using the [setup script](../../tools/setup_scripts/ros2_humble_install.sh).
- Visual Studio Code installed on your computer.

- Install Visual Studio Code Extensions (From the Extensions tab or menu in Visual Studio Code):
  - [Remote - SSH extension](https://marketplace.visualstudio.com/items?itemName=ms-vscode-remote.remote-ssh)
  - [ROS extension pack](https://marketplace.visualstudio.com/items?itemName=ms-iot.vscode-ros)
  - [Python extension](https://marketplace.visualstudio.com/items?itemName=ms-python.python)
  - [C/C++ extension](https://marketplace.visualstudio.com/items?itemName=ms-vscode.cpptools)
  - [CMake Tools extension](https://marketplace.visualstudio.com/items?itemName=ms-vscode.cmake-tools)

## Setup SSH keys for easy access

1. Open a terminal on your computer and create SSH key.

> Skip this step if you already have SSH keys configured.

```bash
# Go to your ssh directory
cd ~/.ssh
# Generate a new SSH key pair
ssh-keygen -t ed25519 -C "your_email@example.com"
# Copy the public key to the robot
ssh-copy-id -i ~/.ssh/id_ed25519.pub username@robot_ip_address
# Test the SSH connection, this should not ask for a password
ssh username@robot_ip_address
```

2. Configure SSH config file for even easier access.

```bash
# Open the SSH config file
nano ~/.ssh/config
```

Add the following lines to the config file, replacing `username` and `robot_ip_address` with your own values.

```bash
Host ttop
    HostName robot_ip_address
    User username
    IdentityFile ~/.ssh/id_ed25519
```

Now you can SSH into the robot using the command `ssh ttop` instead of `ssh username@robot_ip_address`.

## Setup Workspace from Visual Studio Code

1. Open Visual Studio Code and click on the remote_ssh_icon icon in the bottom left corner.
2. Select `Remote-SSH: Connect to Host...` and choose `ttop` from the list.
3. Once connected, open the terminal in Visual Studio Code by clicking on `Terminal` in the top menu and selecting `New Terminal`.
4. In the terminal, we will create a new workspace folder for the project. You can choose any name you like, but for this example, we will use `t_top_ws`. If the directory already exists, create a new one with another name :

```bash
# Create the workspace folder
mkdir -p ~/t_top_ws/src
cd ~/t_top_ws/src
# Clone the repository
git clone https://github.com/introlab/t-top.git --recurse-submodules
```

5. Go back to the root of the workspace to create the colcon configuration file

```bash
# Go to the root of the workspace
cd ~/t_top_ws
# Create the colcon_defaults.yaml file
touch colcon_defaults.yaml
```

6. Open the `colcon_defaults.yaml` file and add the following lines:

```yaml
# colcon_defaults.yaml
build:
  cmake-args:
    - -DCMAKE_EXPORT_COMPILE_COMMANDS=ON
    - --no-warn-unused-cli
    - -DPYTHON_EXECUTABLE=/usr/bin/python3
    - -DCMAKE_BUILD_TYPE=Debug
    - -DCMAKE_CXX_FLAGS=-march=native -ffast-math
    - -DCMAKE_C_FLAGS=-march=native -ffast-math
  symlink-install: true
```

Alternatively, you can copy the sample [colcon_default_jetson.yaml](../../tools/setup_scripts/files/colcon_defaults_jetson.yaml) in your workspace and modify it to fit your needs.

```bash
# Go to the root of the workspace
cd ~/t_top_ws
# Copy the colcon_defaults.yaml file from the t-top repository
cp src/t-top/tools/setup_scripts/files/colcon_defaults_jetson.yaml colcon_defaults.yaml
nano colcon_defaults.yaml
```

7. Build the workspace.

```bash
# Go to the root of the workspace
cd ~/t_top_ws
# Source ROS2 Humble
source /opt/ros/humble/install/setup.bash
# Build the workspace
colcon build
```

## Launch the Control Panel from the Terminal

Control Panel is a graphical interface to test the robot. It allows you to visualize the robot's state, control its movements, and interact with its sensors.

1. Open a terminal in Visual Studio Code and source the workspace.

```bash
# Go to the root of the workspace
cd ~/t_top_ws
# Source ROS2 Humble
source /opt/ros/humble/install/setup.bash
# Source the workspace
source install/setup.bash
```

2. Launch the control panel.

```bash
# Redirect the display to the robot
export DISPLAY=:0
# Launch the control panel
ros2 launch control_panel control_panel.launch.xml
```

Use the multiple tabs in the GUI to test the robot capabilities.

## Remote Development with Visual Studio Code

1. Open Visual Studio Code and click on the remote_ssh_icon icon in the bottom left corner.
2. Select `Remote-SSH: Connect to Host...` and choose `ttop` from the list.
3. Once connected, select `File` in the top menu and select `Open Folder...`.
4. Select the `~/t_top_ws` folder and click "OK".
5. Make sure the `colcon_defaults.yaml` file is in the root of the workspace.
6. Make sure you have the following extensions installed:
   - CMake Tools
   - C/C++
   - Python
   - ROS
7. For autocompletion to work and terminal setup, you must configure the ROS extension and the terminal in the `.vscode/settings.json` file. Open the file and add the following lines:

```json
{
    "ros.rosSetupScript": "/home/introlab/t_top_ws/install/setup.bash",
    "terminal.integrated.profiles.linux": {
        "ROS2 Terminal": {
            "path": "/bin/bash",
            "args": ["-i", "-c", "source /opt/ros/humble/install/setup.bash && source /home/introlab/t_top_ws/install/setup.bash && exec bash"]
        }
    },
    "terminal.integrated.defaultProfile.linux": "ROS2 Terminal"
}
```
If your workspace has a different name than `t_top_ws`, remember to change it both for `ros.rosSetupScript` and `terminal.integrated.profiles.linux` above.

8. Open the terminal in Visual Studio Code by clicking on `Terminal` in the top menu and selecting `New Terminal`.

>The terminal should now be configured to source ROS2 Humble and your workspace setup files automatically.

9. You can now build the workspace using the command `colcon build` in the terminal.

10. You can now run the robot using the command `ros2 launch control_panel control_panel.launch.xml` in the terminal.

## Debugging from Visual Studio Code

Open the workspace folder as described in the previous section.

1. Create a `launch.json` file in the `.vscode` folder.
2. Open the `launch.json` file and add the following lines:

```json
{
    "configurations": [
    {
        "name": "ROS: Launch test nodes",
        "type": "ros",
        "request": "launch",
        "target": "${workspaceFolder}/src/enter-the-full-path-of-your-launch-file",
        "cwd": "${workspaceFolder}",
    }
    ]
}
```

### WARNINGS

1. When debugging, make sure to set the `CMAKE_BUILD_TYPE` to `Debug` in the `colcon_defaults.yaml` file. This will enable debugging symbols and allow you to set breakpoints in your code.

2. When debugging, make sure to set the `PYTHON_EXECUTABLE` to `/usr/bin/python3` in the `colcon_defaults.yaml` file. This will ensure that the correct Python interpreter is used for debugging.

3. When you launch the debugger, **ALL** the nodes in the launch file will be launched. This means that if you set a breakpoint in one node, all the other nodes will be launched and will run until the breakpoint is hit. This can cause issues if you have multiple nodes that are not designed to run together. To avoid this, you can create a separate launch file for debugging that only launches the node you want to debug.

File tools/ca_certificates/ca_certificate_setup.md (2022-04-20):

# Generating CA Certificates for the robot

## 1. Generate CA Certificates on the robot
You need to generate a CA certificate for the robot to allow for HTTPS connections to the robot on the local network.
It will be tied to its IP address on the LAN, so make sure to give the robot a static IP address before generating the certificate.
Make sure to replace the `<IP_ADDRESS_OF_THE_ROBOT>` placeholder with the IP address of the robot in the command below.

```bash
# Run this script on the robot
./generate_certificate.sh <IP_ADDRESS_OF_THE_ROBOT>
```

This will need to be done again when the certificate expires, after 365 days.

## 2. Copy the CA certificate to the developpement machine
If the developpement machine is using Ubuntu, you can use a script to install the certificate. The script uses `scp` to copy the certificate to the developpement machine, so you will need the password for the `introlab` user on the robot if you don't have an ssh key setup.
Make sure to replace the `<IP_ADDRESS_OF_THE_ROBOT>` placeholder with the IP address of the robot (for SSH) and the `<NAME_OF_THE_ROBOT>` placeholder with the name of the robot (for the certificate file name, to distinguish it from files from other robots).

```bash
# Run this script on the developpement machine
./fetch_certificate.sh <IP_ADDRESS_OF_THE_ROBOT> <NAME_OF_THE_ROBOT>
```

This step can be done by many developpers without the need to redo step one every time, but it will have to be redone if step 1 is done again.

## 3. Add the CA certificate to your browser
The certificate installed on your system is not enough for your browser to trust it.
You need to add the certificate to your browser.

Open your browser's settings, and find the CA Certificates setting. Add the ca-certificate `/usr/local/share/ca-sertificates/<NAME_OF_THE_ROBOT>-ca-cert.crt` as a trusted certificate.

### Firefox
1. Open the Preferences menu
2. Search for "certif"
3. Click on the "Show Certificates" button
4. Go to the "Authorities" tab
5. Click on the "Import" button
6. Select the certificate file

### Chromium (Chrome, Brave, etc.)
1. Navigate to the URL  ̀chrome://settings/certificates`
2. Go to the "Authorities" tab
3. Click on the "Import" button
4. Select the certificate file

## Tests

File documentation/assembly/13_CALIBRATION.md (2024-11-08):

# Calibration

## A. 2D Wide Camera

1. Execute the following command.
```bash
ros2 launch t_top platform.launch.xml camera_2d_wide_enabled:=true
```
2. Follow the following [steps](http://wiki.ros.org/camera_calibration/Tutorials/MonocularCalibration).
```bash
# Create calibration path
mkdir -p ~/.ros/t-top/calibration
ros2 run camera_calibration cameracalibrator --size 9x6 --square 0.051 --ros-args -r image:=/camera_2d_wide_full_hd/image -r camera/set_camera_info:=/camera_2d_wide_full_hd/set_camera_info
```

## B. sound_object_person_following

1. Place an object having visual features in front of the robot.
2. Execute the following command.
```bash
ros2 launch sound_object_person_following calibrate_sound_object_person_following.launch.xml
```

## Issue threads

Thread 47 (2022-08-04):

Version 4

mamaheux, 2022-08-04:
- [ ] NVIDIA Jetson AGX Orin
- [ ] LEDs around the base (WS2812B, 30 LEDs / m)
- [ ] Replace discrete LEDs by a strip (WS2812B, 144 LEDs / m)
- [ ] Touch sensors around the base (IS31SE5111)

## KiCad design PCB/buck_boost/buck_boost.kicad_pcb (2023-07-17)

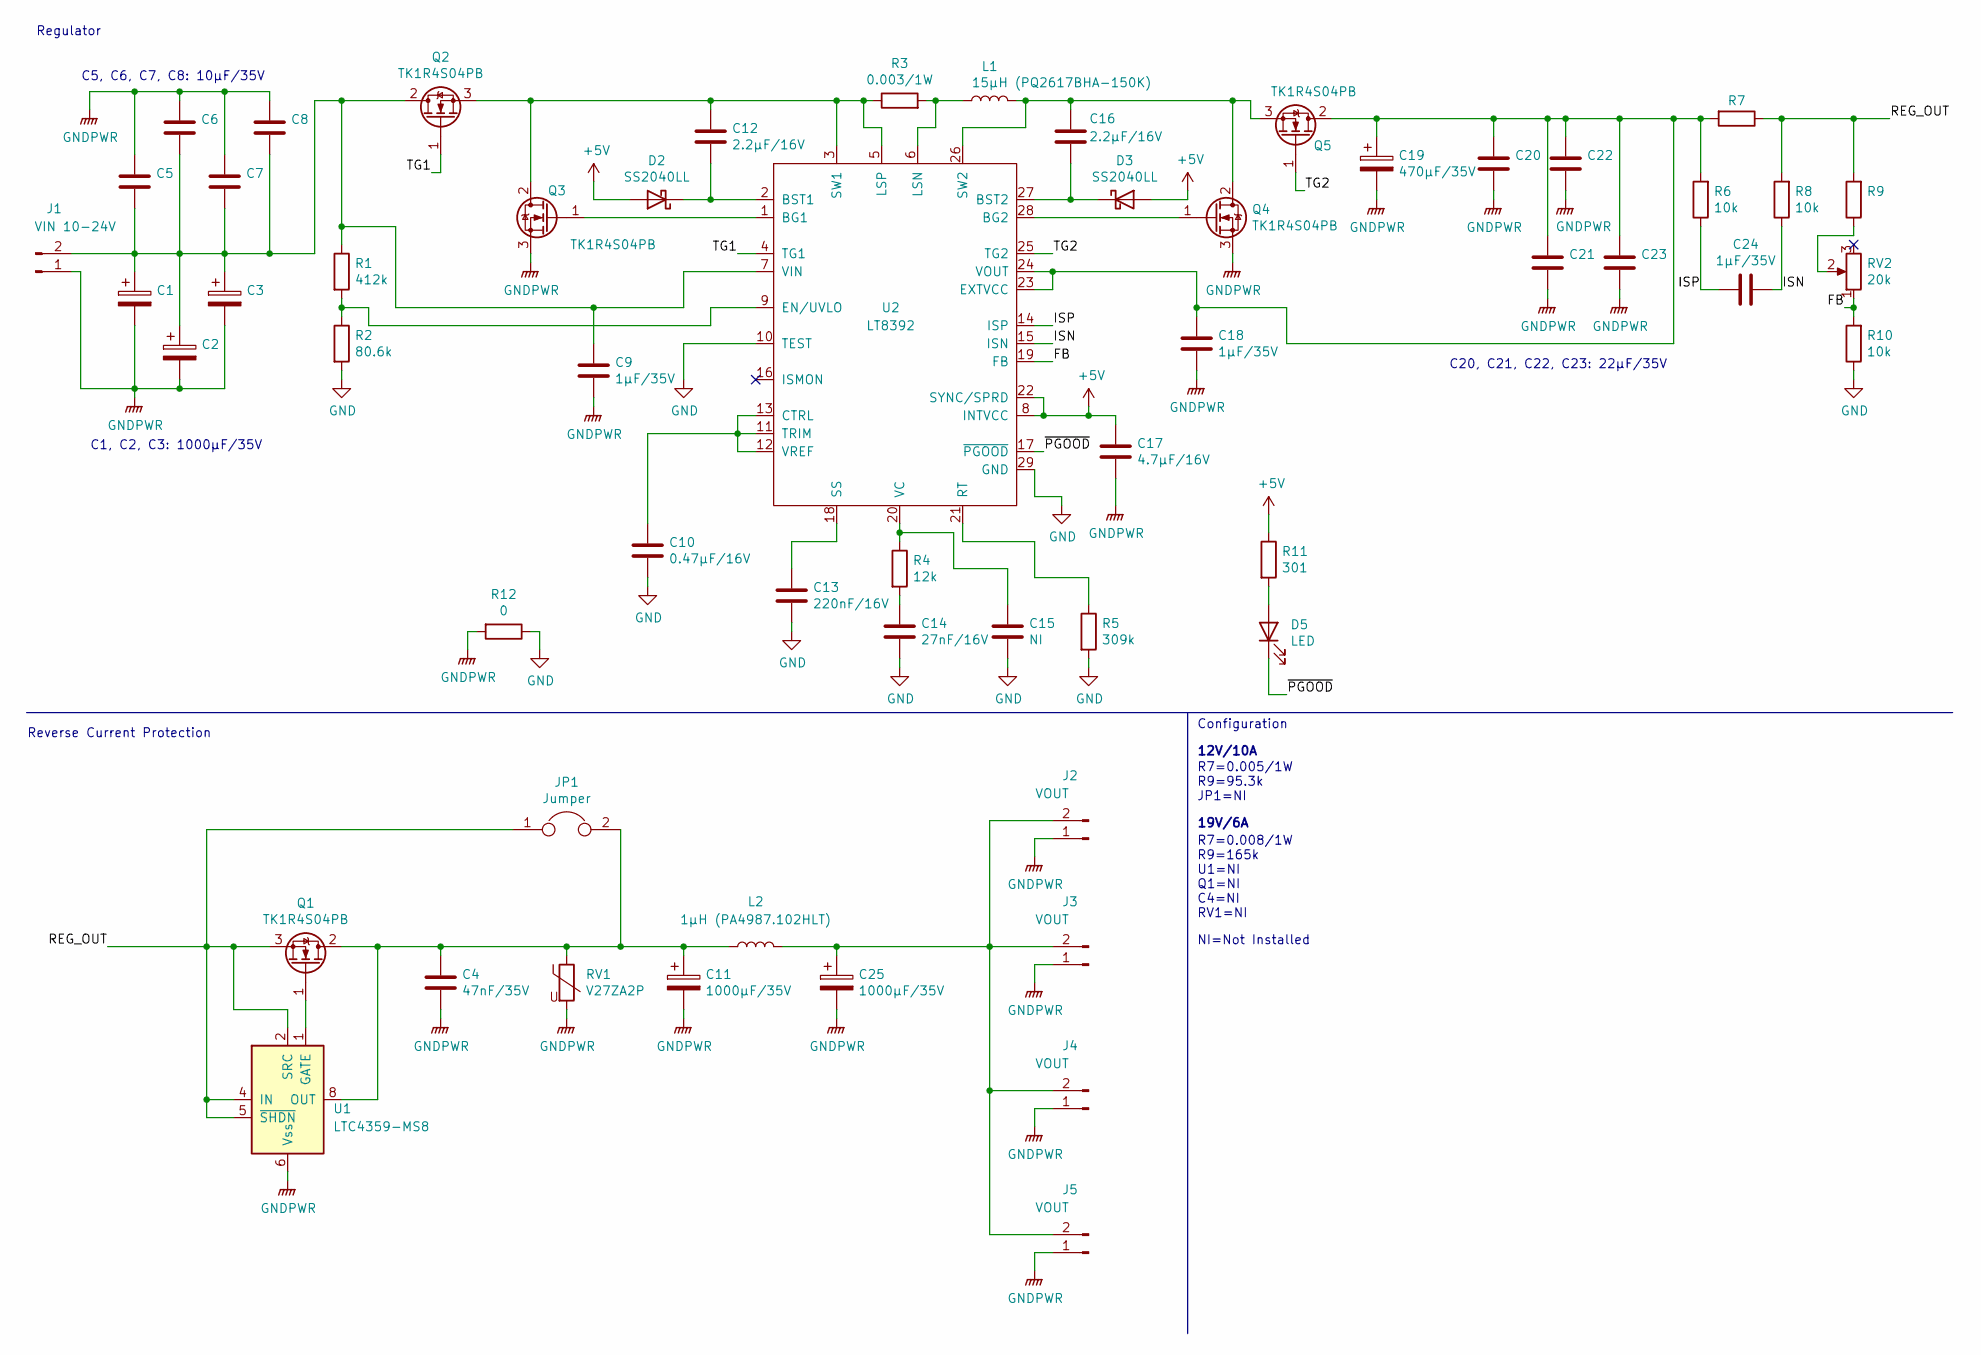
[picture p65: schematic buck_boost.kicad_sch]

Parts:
C1, C2, C3, C11, C25: 1000µF/35V; CP_Radial_D12.5mm_P5.00mm
C4: 47nF/35V; C_0805_2012Metric
C5, C6, C7, C8: 10µF/35V; C_1206_3216Metric
C9, C18, C24: 1µF/35V; C_0805_2012Metric
C10: 0.47µF/16V; C_0805_2012Metric
C12, C16: 2.2µF/16V; C_0805_2012Metric
C13: 220nF/16V; C_0805_2012Metric
C14: 27nF/16V; C_0805_2012Metric
C15: NI; C_0805_2012Metric
C17: 4.7µF/16V; C_0805_2012Metric
C19: 470µF/35V; CP_Radial_D12.5mm_P5.00mm
C20, C21, C22, C23: 22µF/35V; C_1206_3216Metric
D2, D3: SS2040LL; D_SOD-123F
D5: LED; D_0805_2012Metric
J1: VIN 10-24V; OSTTA020161
J2, J3, J4, J5: VOUT; OSTTA020161
JP1: Jumper; R_1206_3216Metric
L1: 15µH (PQ2617BHA-150K); PQ2617BHA-150K
L2: 1µH (PA4987.102HLT); PA4987.XXXHL
Q1, Q2, Q3, Q4, Q5: TK1R4S04PB; TO-252-2
R1: 412k; R_0805_2012Metric
R2: 80.6k; R_0805_2012Metric
R3: 0.003/1W; R_1206_3216Metric
R4: 12k; R_0805_2012Metric
R5: 309k; R_0805_2012Metric
R6, R8, R10: 10k; R_0805_2012Metric
R7: RIS; R_1206_3216Metric
R9: FB3; R_0805_2012Metric
R11: 301; R_0805_2012Metric
R12: 0; R_1206_3216Metric
RV1: V27ZA2P; RV_Disc_D12mm_W4.2mm_P7.5mm
RV2: 20k; Potentiometer_Bourns_3296W_Vertical
U1: LTC4359-MS8; MSOP-8_3x3mm_P0.65mm
U2: LT8392; TSSOP-28-1EP_4.4x9.7mm_P0.65mm

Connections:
+5V: C17.1, D2.2 (A), D3.2 (A), R11.1, U2.8 (INTVCC), U2.22 (SYNC/SPRD)
/FB: R10.2, RV2.1, U2.19 (FB)
/ISN: C24.1, R8.1, U2.15 (ISN)
/ISP: C24.2, R6.1, U2.14 (ISP)
/REG_OUT: JP1.1, Q1.3 (S), R7.1, R8.2, R9.2, U1.2 (SRC), U1.4 (IN), U1.5 (~SHDN)
/TG1: Q2.1 (G), U2.4 (TG1)
/TG2: Q5.1 (G), U2.25 (TG2)
/~PGOOD: D5.1 (K), U2.17 (~PGOOD)
GND: C10.2, C13.2, C14.2, C15.2, R2.2, R5.2, R10.1, R12.1, U2.10 (TEST), U2.29 (GND)
GNDPWR: C1.2, C2.2, C3.2, C4.2, C5.1, C6.1, C7.1, C8.1, C9.2, C11.2, C17.2, C18.2, C19.2, C20.2, C21.2, C22.2, C23.2, C25.2, J1.1, J2.1, J3.1, J4.1, J5.1, Q3.3 (S), Q4.3 (S), R12.2, RV1.2, U1.6 (Vss)
unnamed: C1.1, C2.1, C3.1, C5.2, C6.2, C7.2, C8.2, C9.1, J1.2, Q2.2 (D), R1.1, U2.7 (VIN)
unnamed: C10.1, U2.11 (TRIM), U2.12 (VREF), U2.13 (CTRL)
unnamed: C4.1, C11.1, JP1.2, L2.1, Q1.2 (D), RV1.1, U1.8 (OUT)
unnamed: C12.1, Q2.3 (S), Q3.2 (D), R3.1, U2.3 (SW1), U2.5 (LSP)
unnamed: C12.2, D2.1 (K), U2.2 (BST1)
unnamed: C13.1, U2.18 (SS)
unnamed: C14.1, R4.2
unnamed: C15.1, R4.1, U2.20 (VC)
unnamed: C16.1, L1.2, Q4.2 (D), Q5.3 (S), U2.26 (SW2)
unnamed: C16.2, D3.1 (K), U2.27 (BST2)
unnamed: C18.1, C19.1, C20.1, C21.1, C22.1, C23.1, Q5.2 (D), R6.2, R7.2, U2.23 (EXTVCC), U2.24 (VOUT)
unnamed: C25.1, J2.2, J3.2, J4.2, J5.2, L2.2
unnamed: D5.2 (A), R11.2
unnamed: L1.1, R3.2, U2.6 (LSN)
unnamed: Q1.1 (G), U1.1 (GATE)
unnamed: Q3.1 (G), U2.1 (BG1)
unnamed: Q4.1 (G), U2.28 (BG2)
unnamed: R1.2, R2.1, U2.9 (EN/UVLO)
unnamed: R5.1, U2.21 (RT)
unnamed: R9.1, RV2.2

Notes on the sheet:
NI=Not Installed
12V/10A
Configuration
Regulator
C5, C6, C7, C8: 10µF/35V
R7=0.005/1W R9=95.3k JP1=NI
Reverse Current Protection
C20, C21, C22, C23: 22µF/35V
R7=0.008/1W R9=165k U1=NI Q1=NI C4=NI RV1=NI
19V/6A
C1, C2, C3: 1000µF/35V

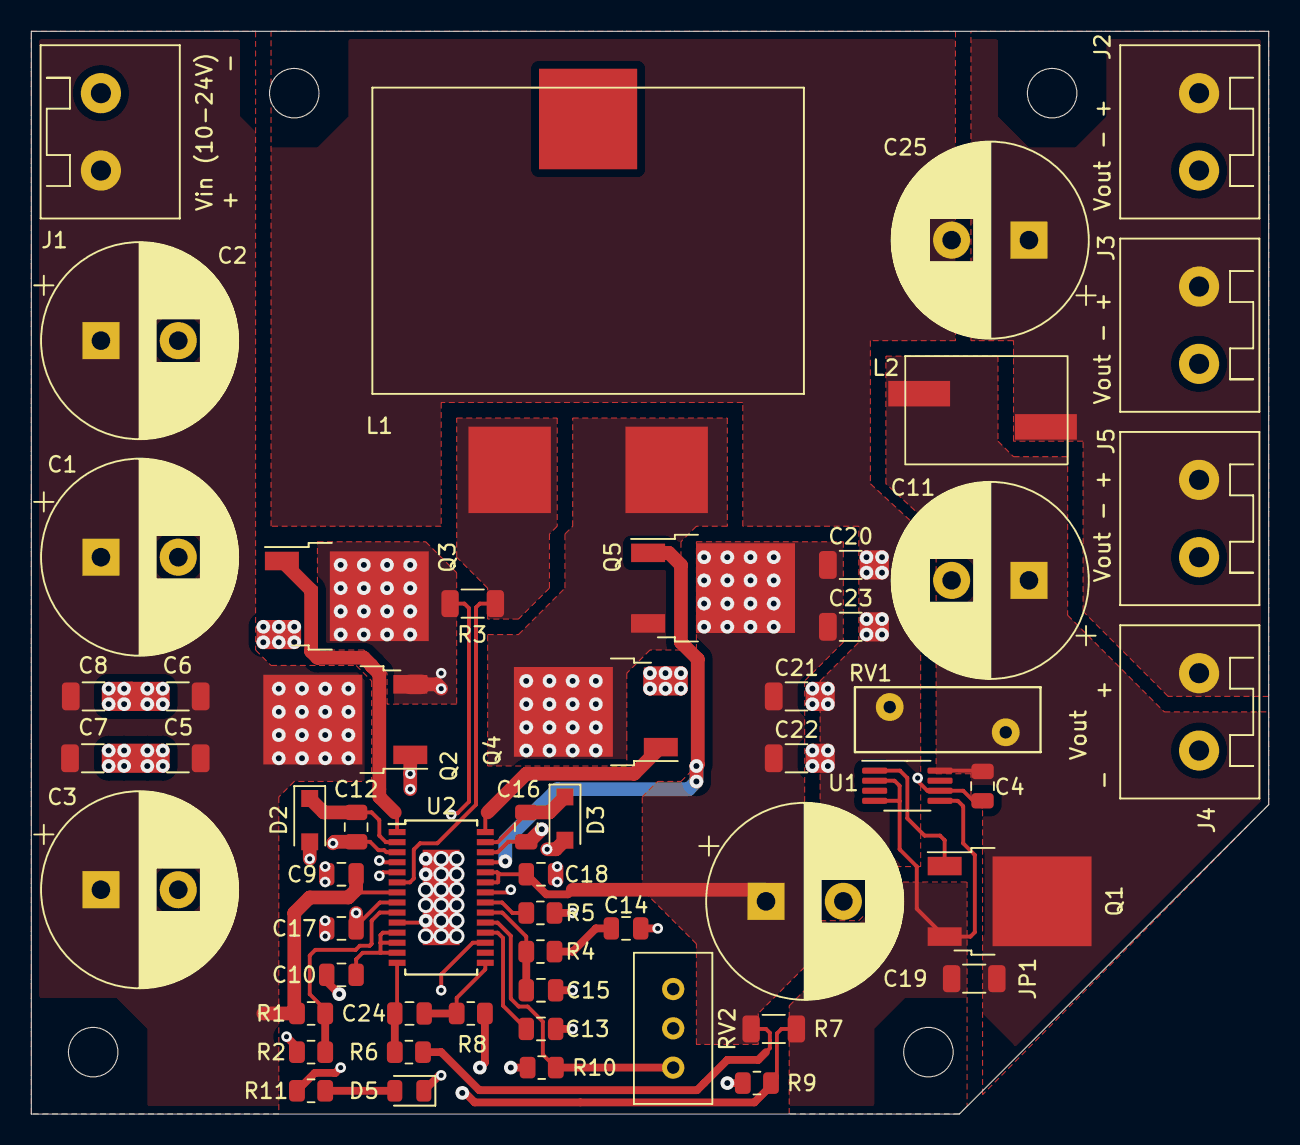
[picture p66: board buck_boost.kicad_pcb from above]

Board: 4 copper layers, 80.0 x 70.0 mm, 57 parts (1 on the bottom side), 30 nets.

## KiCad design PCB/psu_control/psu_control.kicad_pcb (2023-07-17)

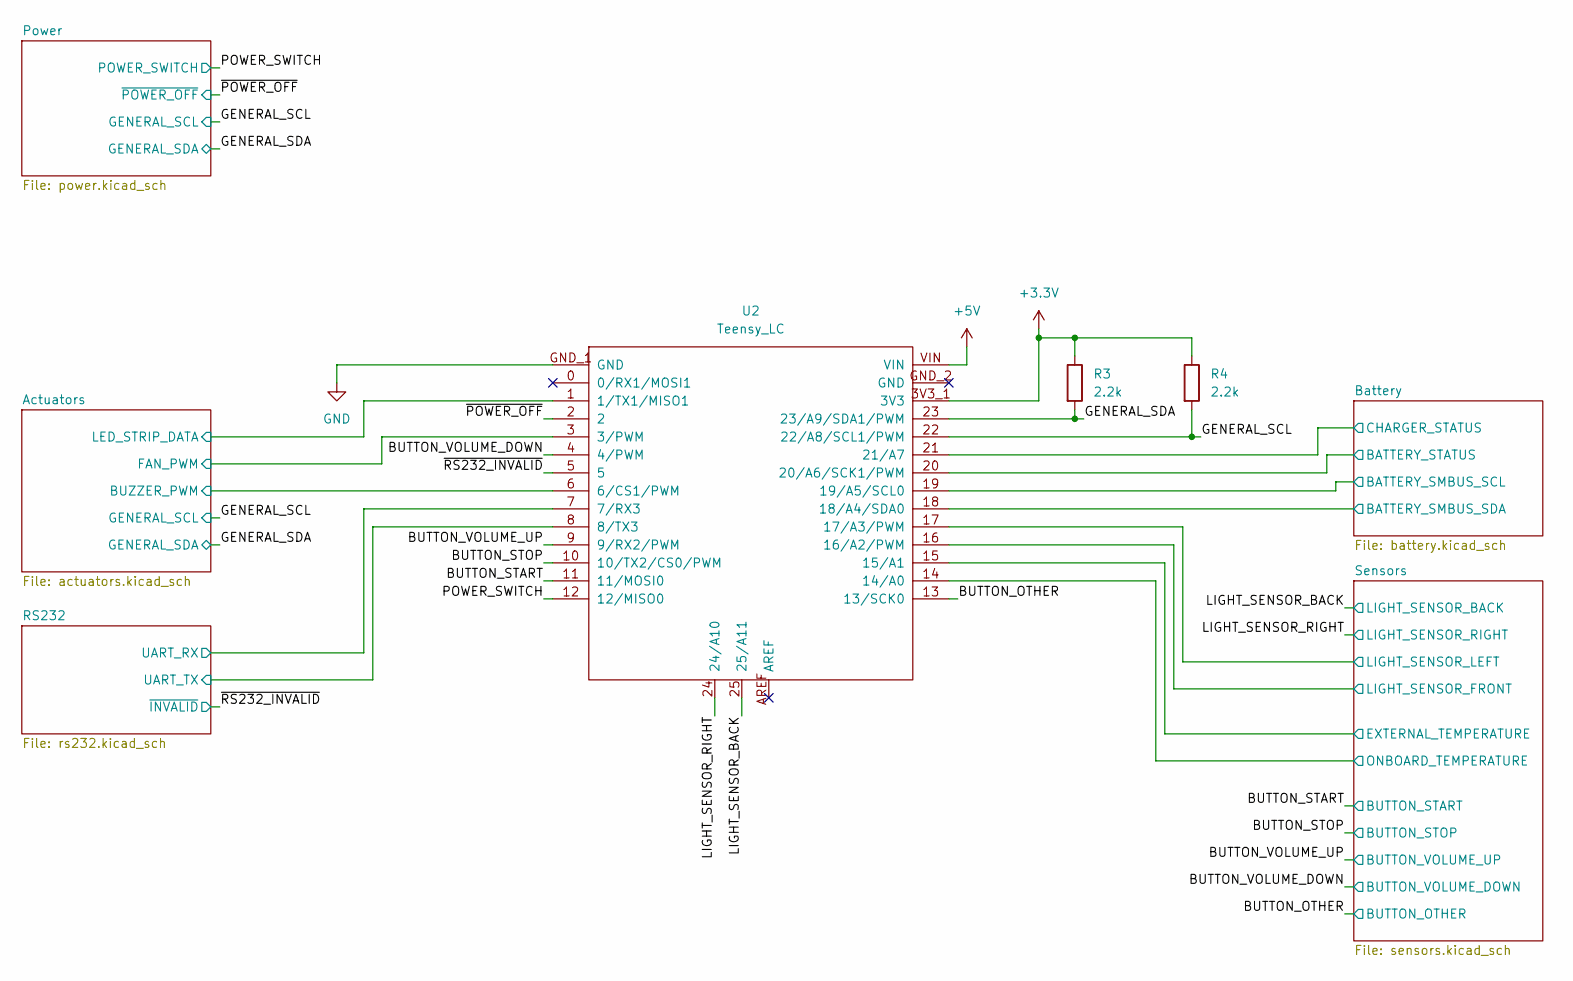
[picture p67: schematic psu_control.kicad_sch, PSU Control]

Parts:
R3, R4: 2.2k; R_0805_2012Metric
U2: Teensy_LC

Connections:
+3.3V: R3.1, R4.1, U2.3V3_1 (3V3); also elsewhere on the board
+5V: U2.VIN; also elsewhere on the board
/Actuators/BUZZER_PWM: U2.6 (6/CS1/PWM); also elsewhere on the board
/Actuators/FAN_PWM: U2.3 (3/PWM); also elsewhere on the board
/Actuators/LED_STRIP_DATA: U2.1 (1/TX1/MISO1); also elsewhere on the board
/BUTTON_OTHER: U2.13 (13/SCK0); also elsewhere on the board
/BUTTON_START: U2.11 (11/MOSI0); also elsewhere on the board
/BUTTON_STOP: U2.10 (10/TX2/CS0/PWM); also elsewhere on the board
/BUTTON_VOLUME_DOWN: U2.4 (4/PWM); also elsewhere on the board
/BUTTON_VOLUME_UP: U2.9 (9/RX2/PWM); also elsewhere on the board
/Battery/BATTERY_SMBUS_SCL: U2.19 (19/A5/SCL0); also elsewhere on the board
/Battery/BATTERY_SMBUS_SDA: U2.18 (18/A4/SDA0); also elsewhere on the board
/Battery/BATTERY_STATUS: U2.20 (20/A6/SCK1/PWM); also elsewhere on the board
/Battery/CHARGER_STATUS: U2.21 (21/A7); also elsewhere on the board
/GENERAL_SCL: R4.2, U2.22 (22/A8/SCL1/PWM); also elsewhere on the board
/GENERAL_SDA: R3.2, U2.23 (23/A9/SDA1/PWM); also elsewhere on the board
/LIGHT_SENSOR_BACK: U2.25 (25/A11); also elsewhere on the board
/LIGHT_SENSOR_RIGHT: U2.24 (24/A10); also elsewhere on the board
/POWER_SWITCH: U2.12 (12/MISO0); also elsewhere on the board
/RS232/UART_RX: U2.7 (7/RX3); also elsewhere on the board
/RS232/UART_TX: U2.8 (8/TX3); also elsewhere on the board
/Sensors/EXTERNAL_TEMPERATURE: U2.15 (15/A1); also elsewhere on the board
/Sensors/LIGHT_SENSOR_FRONT: U2.16 (16/A2/PWM); also elsewhere on the board
/Sensors/LIGHT_SENSOR_LEFT: U2.17 (17/A3/PWM); also elsewhere on the board
/Sensors/ONBOARD_TEMPERATURE: U2.14 (14/A0); also elsewhere on the board
/~POWER_OFF: U2.2; also elsewhere on the board
/~RS232_INVALID: U2.5; also elsewhere on the board
GND: U2.GND_1 (GND); also elsewhere on the board

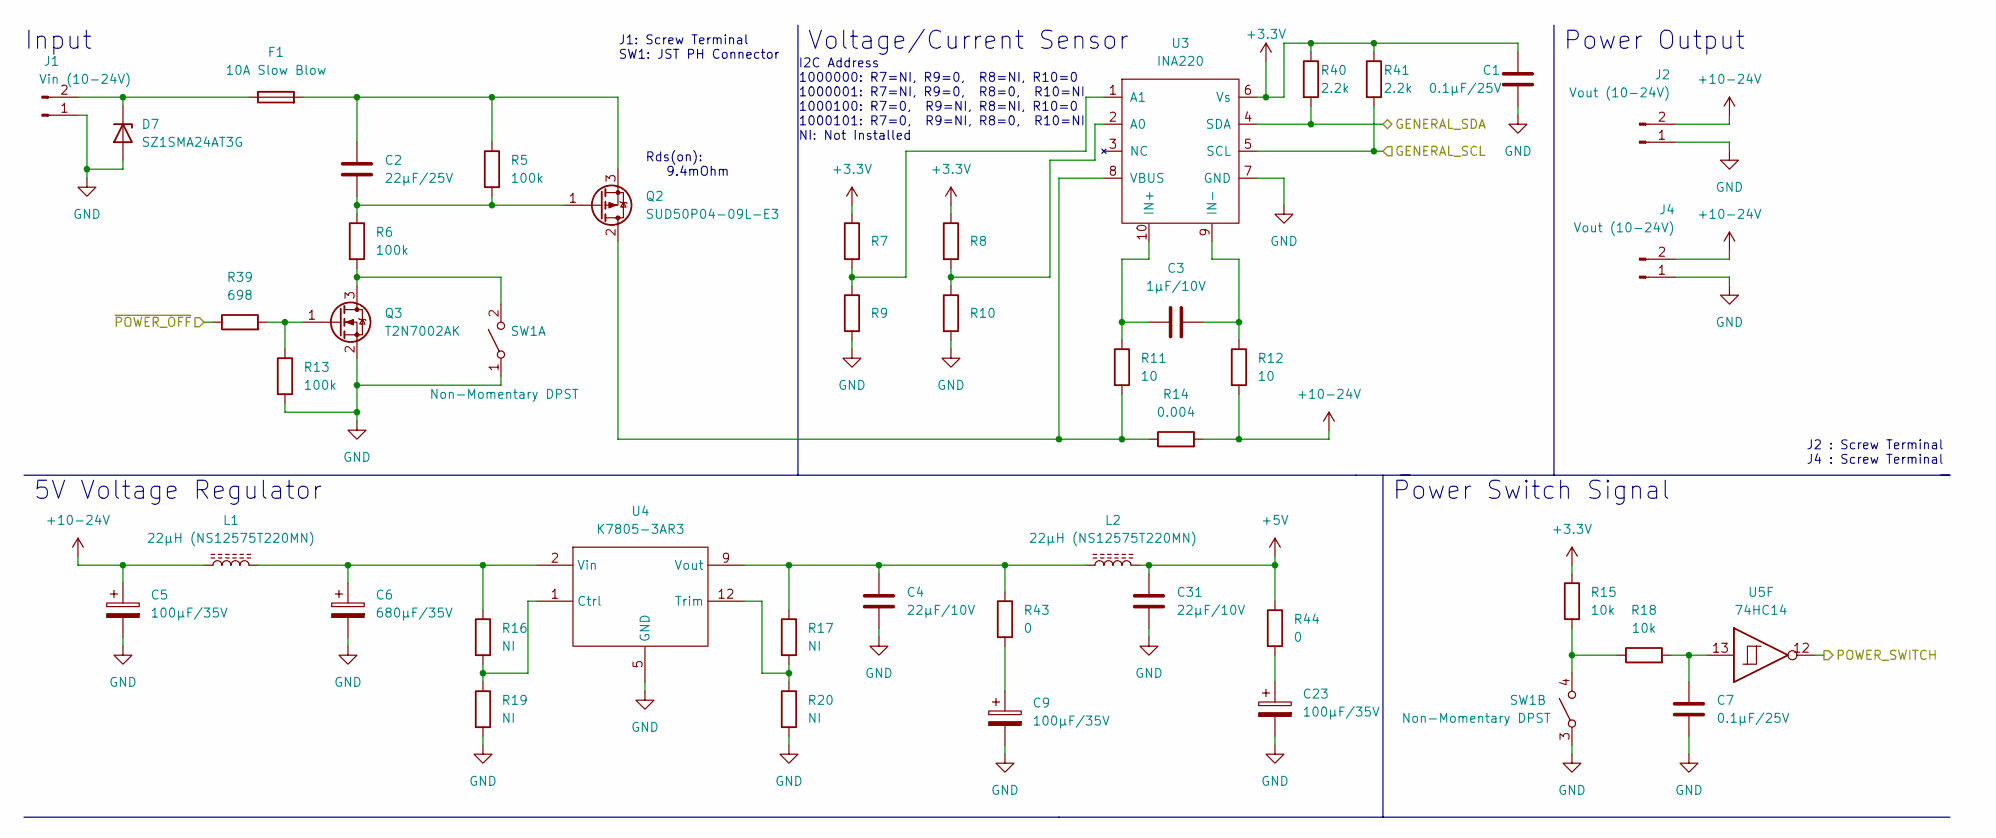
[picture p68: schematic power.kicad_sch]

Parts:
C1, C7: 0.1µF/25V; C_0805_2012Metric
C2: 22µF/25V; C_0805_2012Metric
C3: 1µF/10V; C_0805_2012Metric
C4, C31: 22μF/10V; C_0805_2012Metric
C5, C9, C23: 100µF/35V; CP_Radial_D6.3mm_P2.50mm
C6: 680µF/35V; CP_Radial_D10.0mm_P5.00mm
D7: SZ1SMA24AT3G; D_SMA
F1: 10A Slow Blow; M205_FUSE
J1: Vin (10-24V); OSTTA020161
J2, J4: Vout (10-24V); OSTTA020161
L1, L2: 22µH (NS12575T220MN); NS12575T220MN
Q2: SUD50P04-09L-E3; TO-252-2
Q3: T2N7002AK; SOT-23
R5, R6, R13: 100k; R_0805_2012Metric
R7, R8, R9, R10: 0; R_0805_2012Metric
R11, R12: 10; R_0805_2012Metric
R14: 0.004; R_1206_3216Metric
R15, R18: 10k; R_0805_2012Metric
R16, R17, R19, R20: NI; R_0805_2012Metric
R39: 698; R_0805_2012Metric
R40, R41: 2.2k; R_0805_2012Metric
R43, R44: 0; R_1206_3216Metric
SW1: Non-Momentary DPST; JST_PH_B4B-PH-K_1x04_P2.00mm_Vertical
U3: INA220; VSSOP-10_3x3mm_P0.5mm
U4: K7805-3AR3
U5: 74HC14; TSSOP-14_4.4x5mm_P0.65mm

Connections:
10-25V: C5.1, J2.2, J4.2, L1.1, R12.2, R14.2
+3.3V: C1.1, R7.1, R8.1, R15.1, R40.1, R41.1, U3.6 (Vs); also elsewhere on the board
+5V: C31.1, L2.2, R44.1; also elsewhere on the board
/GENERAL_SCL: R41.2, U3.5 (SCL); also elsewhere on the board
/GENERAL_SDA: R40.2, U3.4 (SDA); also elsewhere on the board
/POWER_SWITCH: U5.12; also elsewhere on the board
/~POWER_OFF: R39.1; also elsewhere on the board
GND: C1.2, C4.2, C5.2, C6.2, C7.2, C9.2, C23.2, C31.2, D7.2 (A), J1.1, J2.1, J4.1, Q3.2 (S), R9.2, R10.2, R13.2, R19.2, R20.2, SW1.1 (A), SW1.3 (A), U3.7 (GND), U4.5 (GND); also elsewhere on the board
unnamed: C2.1, F1.2, Q2.3 (S), R5.1
unnamed: C2.2, Q2.1 (G), R5.2, R6.1
unnamed: C3.1, R11.1, U3.10 (IN+)
unnamed: C3.2, R12.1, U3.9 (IN-)
unnamed: C4.1, L2.1, R17.1, R43.1, U4.9 (Vout)
unnamed: C6.1, L1.2, R16.1, U4.2 (Vin)
unnamed: C7.1, R18.2, U5.13
unnamed: C9.1, R43.2
unnamed: C23.1, R44.2
unnamed: D7.1 (K), F1.1, J1.2
unnamed: Q2.2 (D), R11.2, R14.1, U3.8 (VBUS)
unnamed: Q3.1 (G), R13.1, R39.2
unnamed: Q3.3 (D), R6.2, SW1.2 (B)
unnamed: R7.2, R9.1, U3.1 (A1)
unnamed: R8.2, R10.1, U3.2 (A0)
unnamed: R15.2, R18.1, SW1.4 (B)
unnamed: R16.2, R19.1, U4.1 (Ctrl)
unnamed: R17.2, R20.1, U4.12 (Trim)

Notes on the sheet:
Input
Power Output
Rds(on): 9.4mOhm
Power Switch Signal
J1: Screw Terminal SW1: JST PH Connector
5V Voltage Regulator
I2C Address 1000000: R7=NI, R9=0, R8=NI, R10=0 1000001: R7=NI, R9=0, R8=0, R10=NI 1000100: R7=0, R9=NI, R8=NI, R10=0 1000101: R7=0, R9=NI, R8=0, R10=NI NI: Not Installed
Voltage/Current Sensor
J2 : Screw Terminal J4 : Screw Terminal

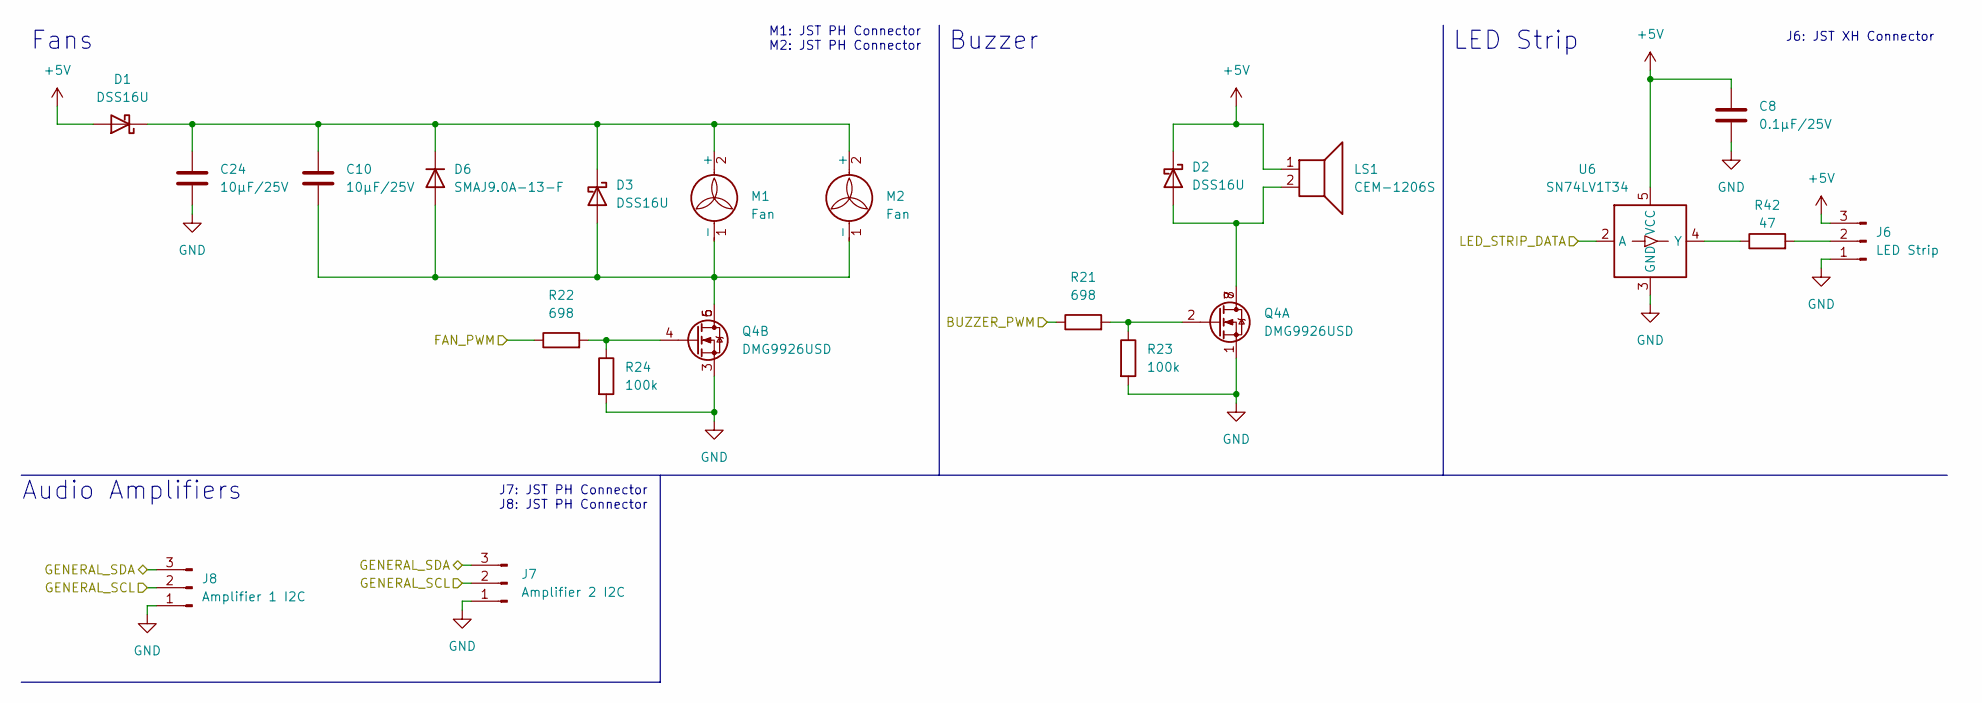
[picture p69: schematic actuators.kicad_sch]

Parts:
C8: 0.1µF/25V; C_0805_2012Metric
C10, C24: 10µF/25V; C_0805_2012Metric
D1, D2, D3: DSS16U; D_SOD-123F
D6: SMAJ9.0A-13-F; D_SMA
J6: LED Strip; JST_XH_B3B-XH-A_1x03_P2.50mm_Vertical
J7: Amplifier 2 I2C; JST_PH_B3B-PH-K_1x03_P2.00mm_Vertical
J8: Amplifier 1 I2C; JST_PH_B3B-PH-K_1x03_P2.00mm_Vertical
LS1: CEM-1206S; WT-1205
M1, M2: Fan; JST_PH_B2B-PH-K_1x02_P2.00mm_Vertical
Q4: DMG9926USD; SOIC-8_3.9x4.9mm_P1.27mm
R21, R22: 698; R_0805_2012Metric
R23, R24: 100k; R_0805_2012Metric
R42: 47; R_0805_2012Metric
U6: SN74LV1T34; SOT-23-5

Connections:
+5V: C8.1, D1.2 (A), D2.1 (K), J6.3, LS1.1, U6.5 (VCC); also elsewhere on the board
/Actuators/BUZZER_PWM: R21.1; also elsewhere on the board
/Actuators/FAN_PWM: R22.1; also elsewhere on the board
/Actuators/LED_STRIP_DATA: U6.2 (A); also elsewhere on the board
/GENERAL_SCL: J7.2, J8.2; also elsewhere on the board
/GENERAL_SDA: J7.3, J8.3; also elsewhere on the board
GND: C8.2, C24.2, J6.1, J7.1, J8.1, Q4.1 (S), Q4.3 (S), R23.2, R24.2, U6.3 (GND); also elsewhere on the board
unnamed: C10.1, C24.1, D1.1 (K), D3.1 (K), D6.1 (K), M1.2 (+), M2.2 (+)
unnamed: C10.2, D3.2 (A), D6.2 (A), M1.1 (-), M2.1 (-), Q4.5 (D), Q4.6 (D)
unnamed: D2.2 (A), LS1.2, Q4.7 (D), Q4.8 (D)
unnamed: J6.2, R42.2
unnamed: Q4.2 (G), R21.2, R23.1
unnamed: Q4.4 (G), R22.2, R24.1
unnamed: R42.1, U6.4 (Y)

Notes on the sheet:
Buzzer
Fans
J6: JST XH Connector
LED Strip
Audio Amplifiers
M1: JST PH Connector M2: JST PH Connector
J7: JST PH Connector J8: JST PH Connector

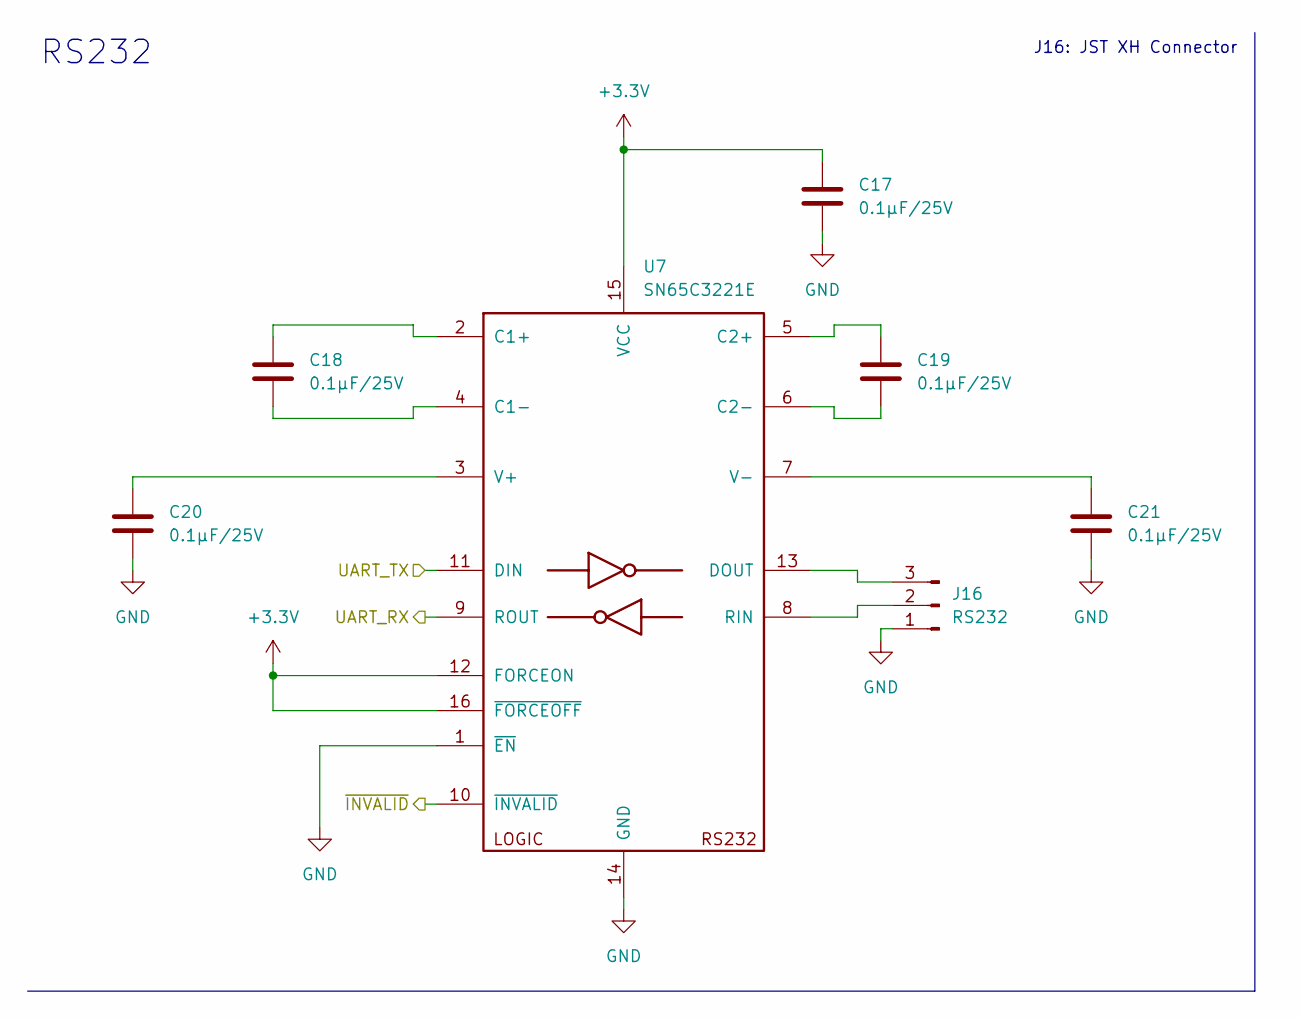
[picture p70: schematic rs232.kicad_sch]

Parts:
C17, C18, C19, C20, C21: 0.1µF/25V; C_0805_2012Metric
J16: RS232; JST_PH_B3B-PH-K_1x03_P2.00mm_Vertical
U7: SN65C3221E; TSSOP-16_4.4x5mm_P0.65mm

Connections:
+3.3V: C17.1, U7.12 (FORCEON), U7.15 (VCC), U7.16 (~FORCEOFF); also elsewhere on the board
/RS232/UART_RX: U7.9 (ROUT); also elsewhere on the board
/RS232/UART_TX: U7.11 (DIN); also elsewhere on the board
/~RS232_INVALID: U7.10 (~INVALID); also elsewhere on the board
GND: C17.2, C20.2, C21.2, J16.1, U7.1 (~EN), U7.14 (GND); also elsewhere on the board
unnamed: C18.1, U7.2 (C1+)
unnamed: C18.2, U7.4 (C1-)
unnamed: C19.1, U7.5 (C2+)
unnamed: C19.2, U7.6 (C2-)
unnamed: C20.1, U7.3 (V+)
unnamed: C21.1, U7.7 (V-)
unnamed: J16.2, U7.8 (RIN)
unnamed: J16.3, U7.13 (DOUT)

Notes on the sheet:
J16: JST XH Connector
RS232

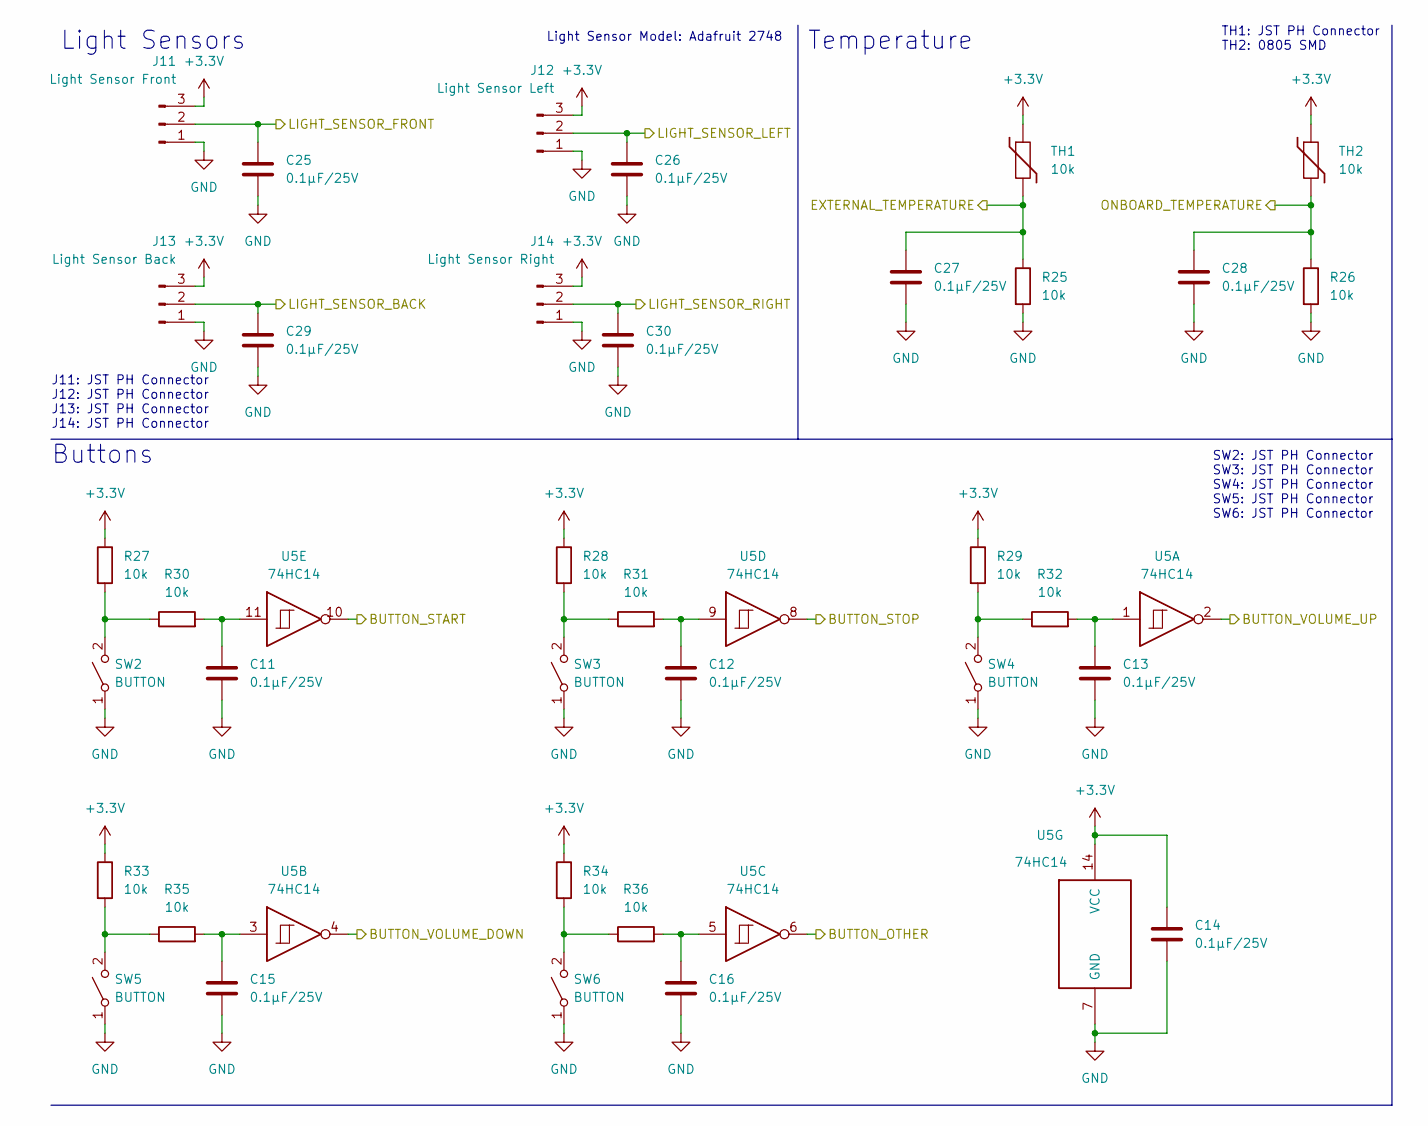
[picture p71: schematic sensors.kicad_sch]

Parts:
C11, C12, C13, C14, C15, C16, C25, C26, C27, C28, C29, C30: 0.1µF/25V; C_0805_2012Metric
J11: Light Sensor Front; JST_PH_B3B-PH-K_1x03_P2.00mm_Vertical
J12: Light Sensor Left; JST_PH_B3B-PH-K_1x03_P2.00mm_Vertical
J13: Light Sensor Back; JST_PH_B3B-PH-K_1x03_P2.00mm_Vertical
J14: Light Sensor Right; JST_PH_B3B-PH-K_1x03_P2.00mm_Vertical
R25, R26, R27, R28, R29, R30, R31, R32, R33, R34, R35, R36: 10k; R_0805_2012Metric
SW2, SW3, SW4, SW5, SW6: BUTTON; JST_PH_B2B-PH-K_1x02_P2.00mm_Vertical
TH1: 10k; JST_PH_B2B-PH-K_1x02_P2.00mm_Vertical
TH2: 10k; R_0805_2012Metric
U5: 74HC14; TSSOP-14_4.4x5mm_P0.65mm

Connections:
+3.3V: C14.1, J11.3, J12.3, J13.3, J14.3, R27.1, R28.1, R29.1, R33.1, R34.1, TH1.1, TH2.1, U5.14 (VCC); also elsewhere on the board
/BUTTON_OTHER: U5.6; also elsewhere on the board
/BUTTON_START: U5.10; also elsewhere on the board
/BUTTON_STOP: U5.8; also elsewhere on the board
/BUTTON_VOLUME_DOWN: U5.4; also elsewhere on the board
/BUTTON_VOLUME_UP: U5.2; also elsewhere on the board
/LIGHT_SENSOR_BACK: C29.1, J13.2; also elsewhere on the board
/LIGHT_SENSOR_RIGHT: C30.1, J14.2; also elsewhere on the board
/Sensors/EXTERNAL_TEMPERATURE: C27.1, R25.1, TH1.2; also elsewhere on the board
/Sensors/LIGHT_SENSOR_FRONT: C25.1, J11.2; also elsewhere on the board
/Sensors/LIGHT_SENSOR_LEFT: C26.1, J12.2; also elsewhere on the board
/Sensors/ONBOARD_TEMPERATURE: C28.1, R26.1, TH2.2; also elsewhere on the board
GND: C11.2, C12.2, C13.2, C14.2, C15.2, C16.2, C25.2, C26.2, C27.2, C28.2, C29.2, C30.2, J11.1, J12.1, J13.1, J14.1, R25.2, R26.2, SW2.1 (A), SW3.1 (A), SW4.1 (A), SW5.1 (A), SW6.1 (A), U5.7 (GND); also elsewhere on the board
unnamed: C11.1, R30.2, U5.11
unnamed: C12.1, R31.2, U5.9
unnamed: C13.1, R32.2, U5.1
unnamed: C15.1, R35.2, U5.3
unnamed: C16.1, R36.2, U5.5
unnamed: R27.2, R30.1, SW2.2 (B)
unnamed: R28.2, R31.1, SW3.2 (B)
unnamed: R29.2, R32.1, SW4.2 (B)
unnamed: R33.2, R35.1, SW5.2 (B)
unnamed: R34.2, R36.1, SW6.2 (B)

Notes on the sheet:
Buttons
SW2: JST PH Connector SW3: JST PH Connector SW4: JST PH Connector SW5: JST PH Connector SW6: JST PH Connector
TH1: JST PH Connector TH2: 0805 SMD
Light Sensors
Temperature
J11: JST PH Connector J12: JST PH Connector J13: JST PH Connector J14: JST PH Connector
Light Sensor Model: Adafruit 2748

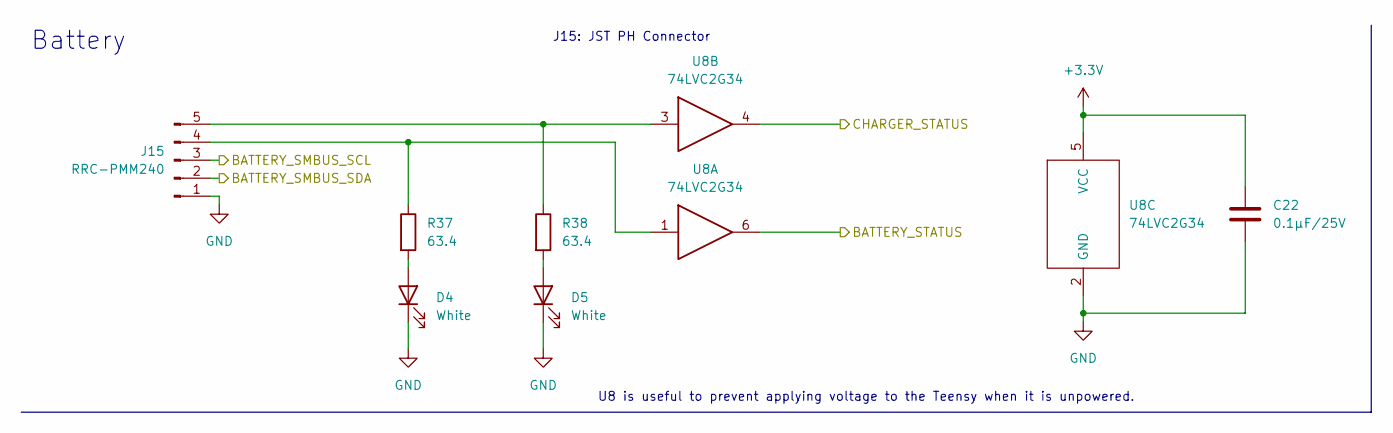
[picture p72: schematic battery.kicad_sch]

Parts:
C22: 0.1µF/25V; C_0805_2012Metric
D4, D5: White; JST_PH_B2B-PH-K_1x02_P2.00mm_Vertical
J15: RRC-PMM240; JST_PH_B5B-PH-K_1x05_P2.00mm_Vertical
R37, R38: 63.4; R_0805_2012Metric
U8: 74LVC2G34; TSOP-6_1.65x3.05mm_P0.95mm

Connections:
+3.3V: C22.1, U8.5 (VCC); also elsewhere on the board
/Battery/BATTERY_SMBUS_SCL: J15.3; also elsewhere on the board
/Battery/BATTERY_SMBUS_SDA: J15.2; also elsewhere on the board
/Battery/BATTERY_STATUS: U8.6; also elsewhere on the board
/Battery/CHARGER_STATUS: U8.4; also elsewhere on the board
GND: C22.2, D4.1 (K), D5.1 (K), J15.1, U8.2 (GND); also elsewhere on the board
unnamed: D4.2 (A), R37.2
unnamed: D5.2 (A), R38.2
unnamed: J15.4, R37.1, U8.1
unnamed: J15.5, R38.1, U8.3

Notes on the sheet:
Battery
U8 is useful to prevent applying voltage to the Teensy when it is unpowered.
J15: JST PH Connector

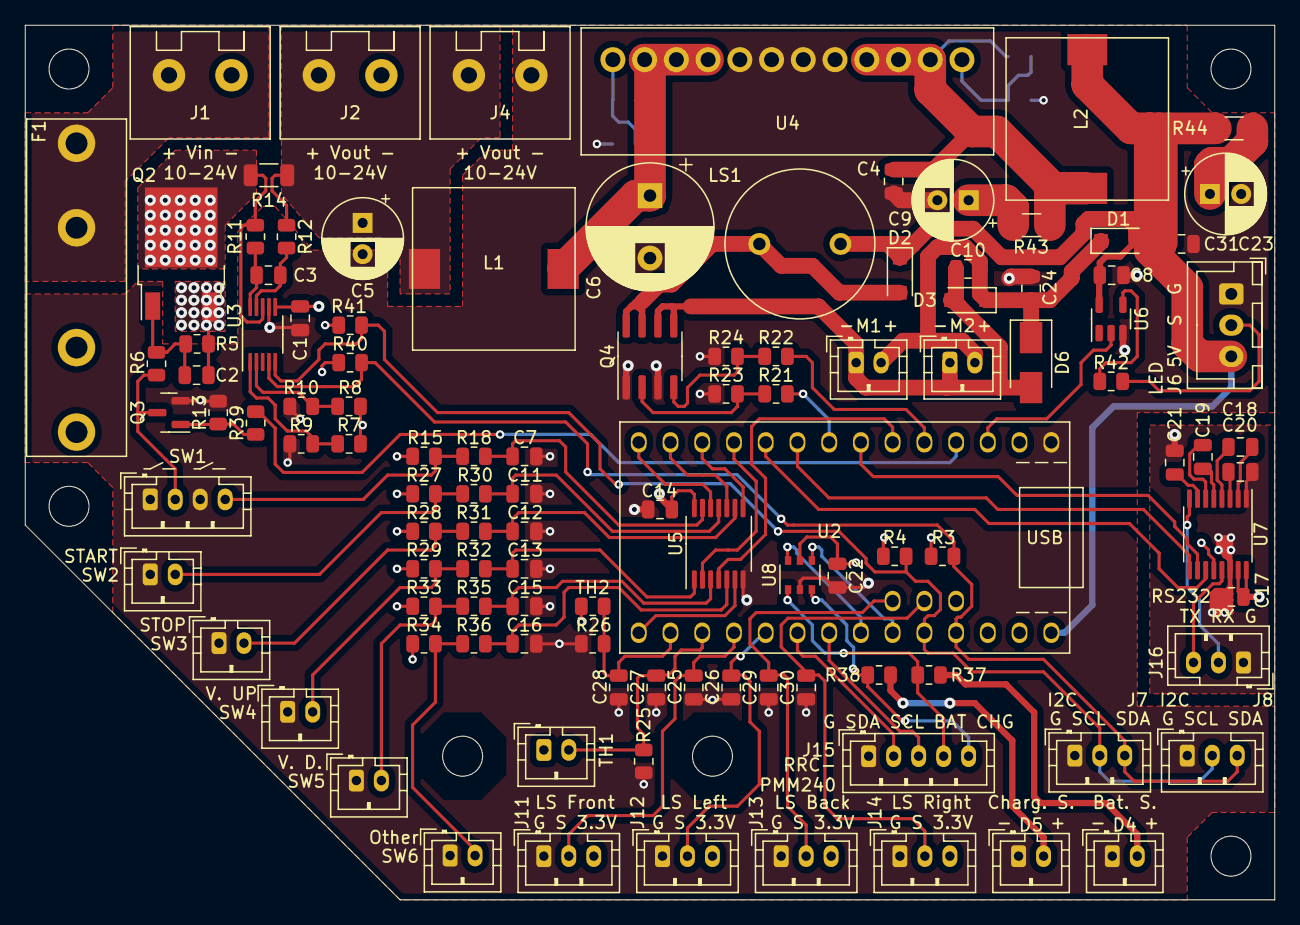
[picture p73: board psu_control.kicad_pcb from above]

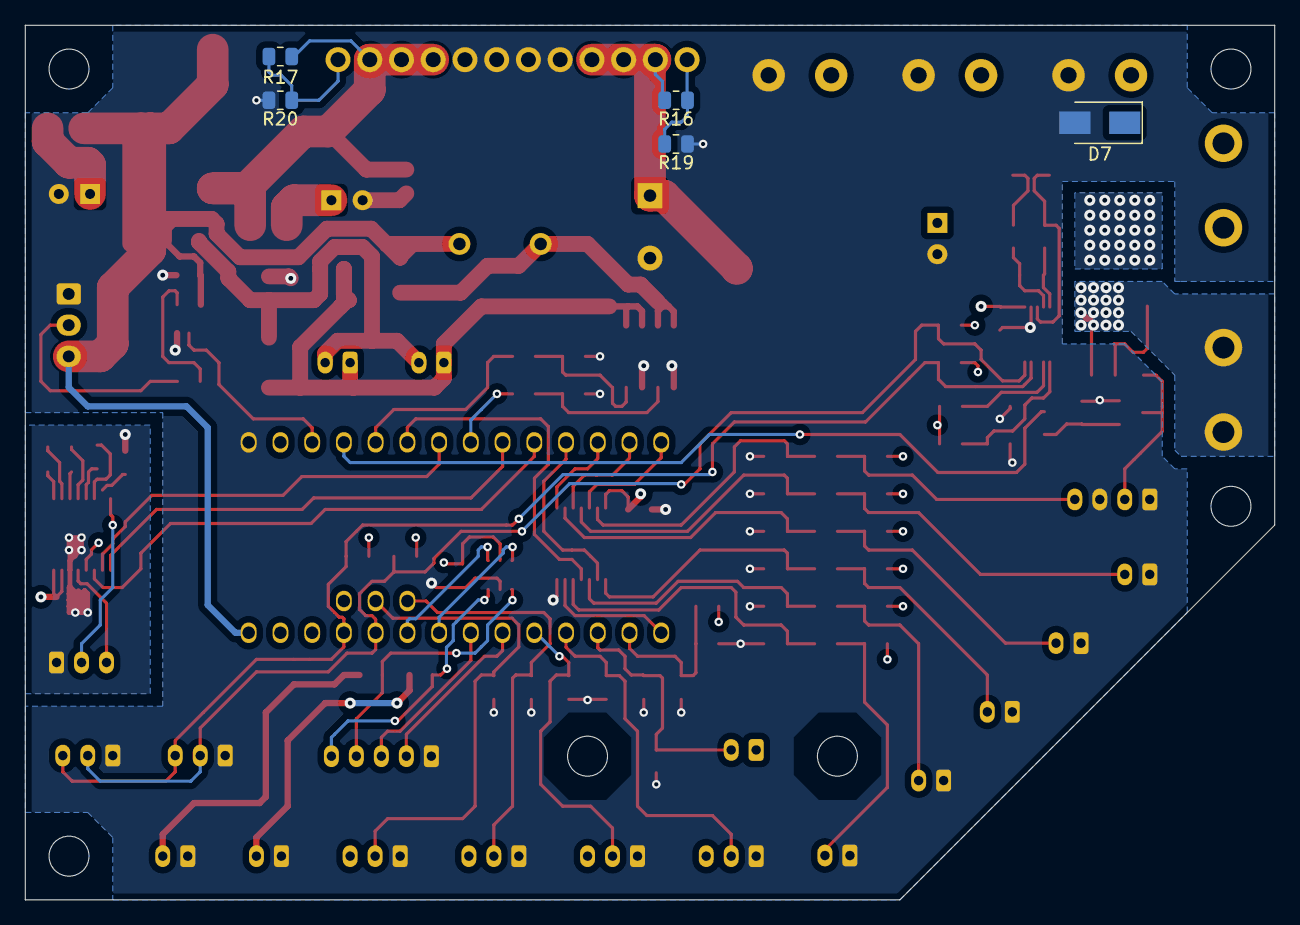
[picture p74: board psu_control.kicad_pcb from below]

Board: 4 copper layers, 100.0 x 70.0 mm, 116 parts (5 on the bottom side), 76 nets.

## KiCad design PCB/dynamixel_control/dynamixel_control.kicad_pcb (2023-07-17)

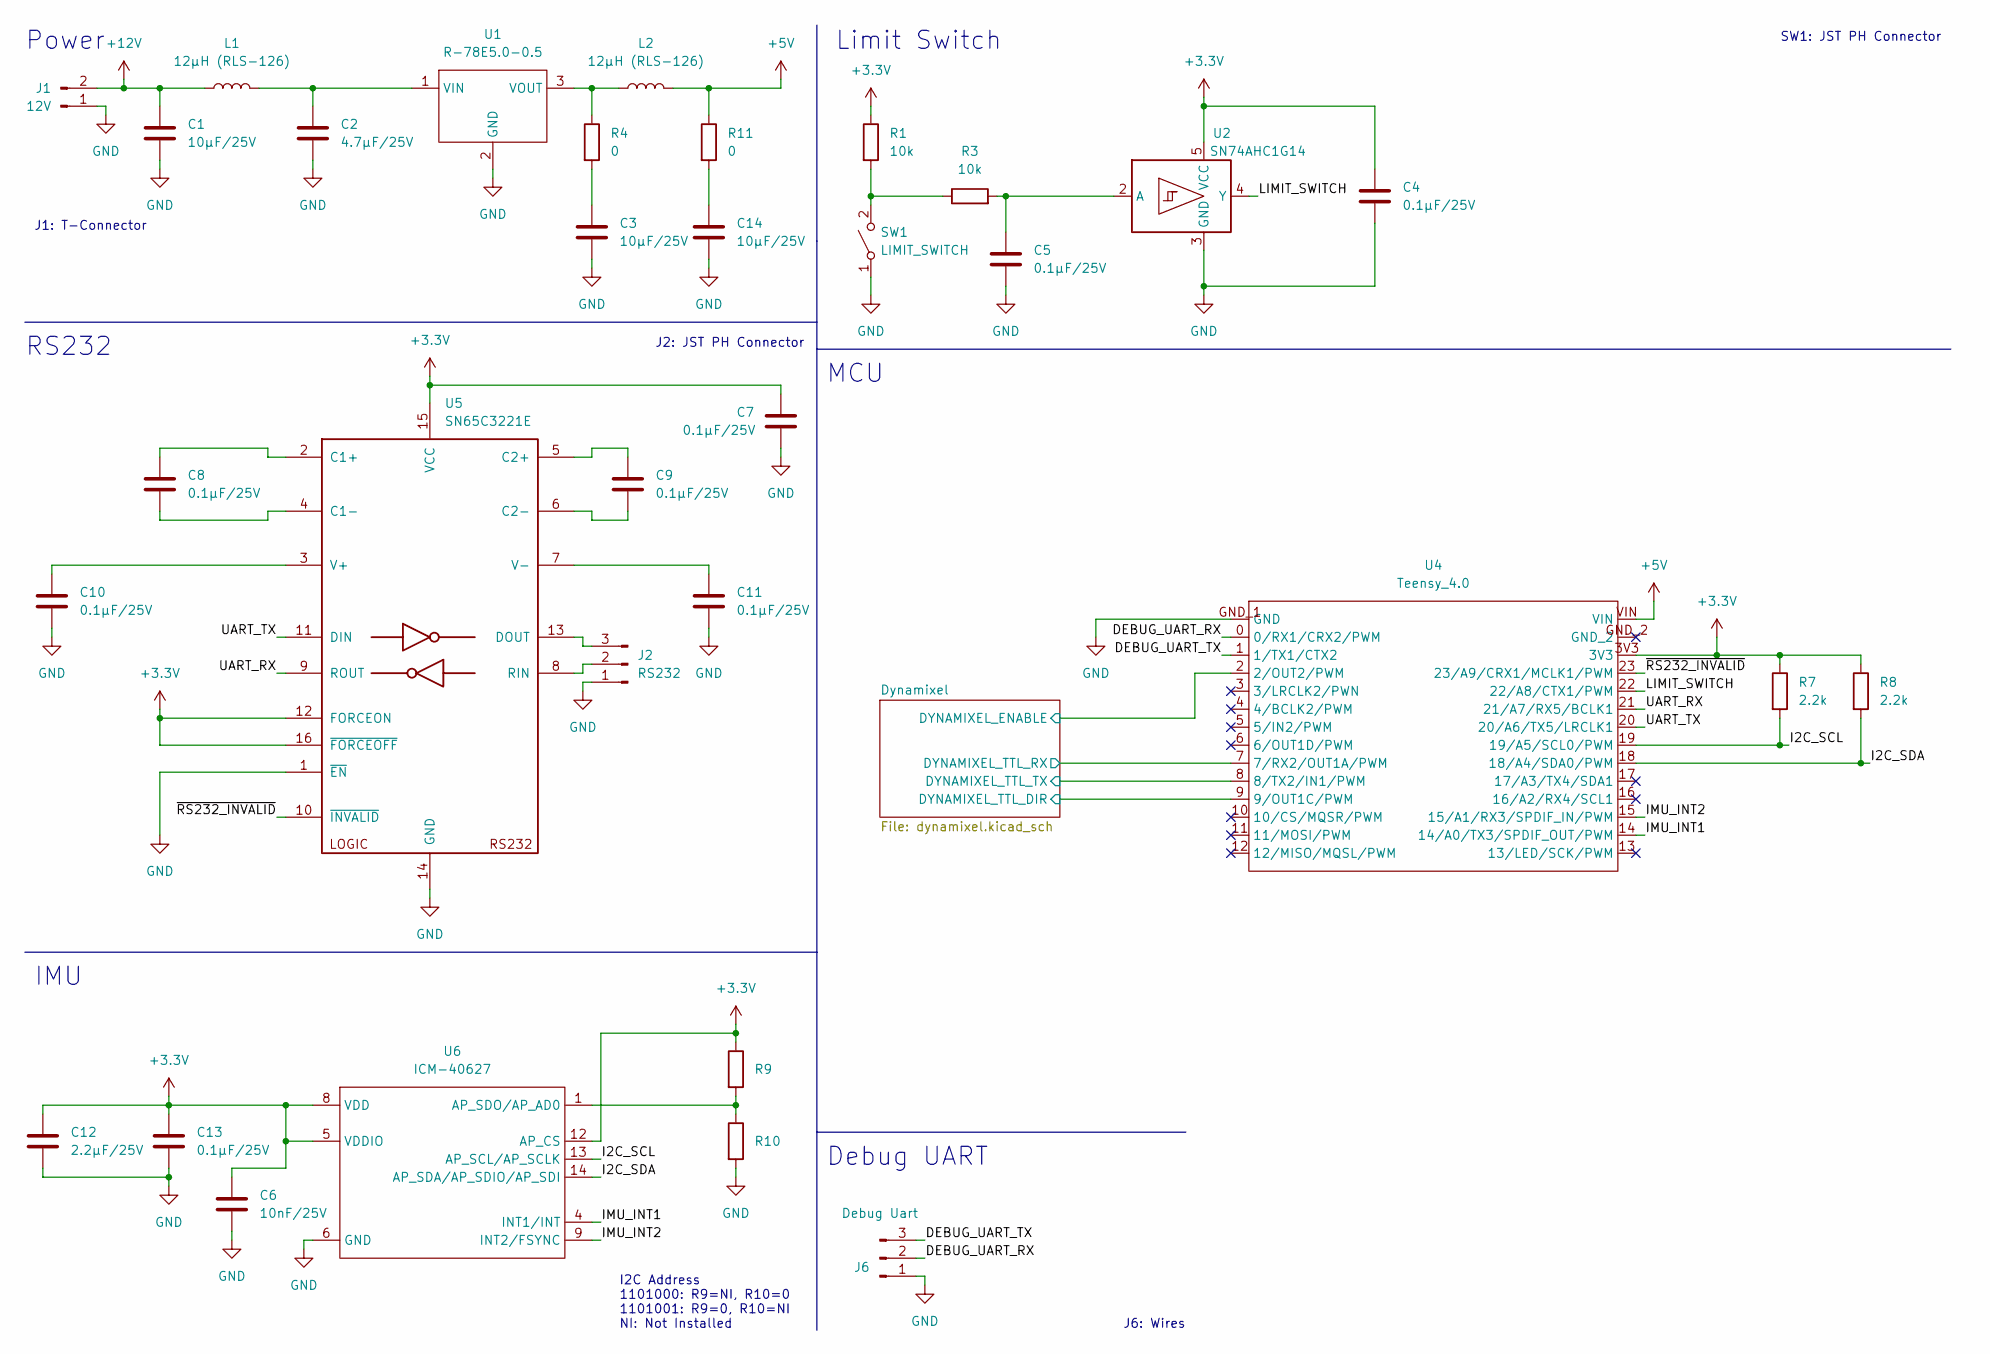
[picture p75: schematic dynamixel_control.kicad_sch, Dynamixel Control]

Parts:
C1, C3, C14: 10µF/25V; C_0805_2012Metric
C2: 4.7µF/25V; C_0805_2012Metric
C4, C5, C7, C8, C9, C10, C11, C13: 0.1µF/25V; C_0805_2012Metric
C6: 10nF/25V; C_0805_2012Metric
C12: 2.2µF/25V; C_0805_2012Metric
J1: 12V; t-connector
J2: RS232; JST_PH_S3B-PH-K_1x03_P2.00mm_Horizontal
J6: Debug Uart; PinHeader_1x03_P1.27mm_Vertical
L1, L2: 12µH (RLS-126); L_1812_4532Metric
R1, R3: 10k; R_0805_2012Metric
R4, R10, R11: 0; R_0805_2012Metric
R7, R8: 2.2k; R_0805_2012Metric
R9: NI; R_0805_2012Metric
SW1: LIMIT_SWITCH; JST_PH_B2B-PH-K_1x02_P2.00mm_Vertical
U1: R-78E5.0-0.5; R-78E-0.5
U2: SN74AHC1G14; SOT-23-5
U4: Teensy_4.0
U5: SN65C3221E; TSSOP-16_4.4x5mm_P0.65mm
U6: ICM-40627

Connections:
+3.3V: C4.1, C6.1, C7.1, C12.1, C13.1, R1.1, R7.1, R8.1, R9.1, U2.5 (VCC), U4.3V3, U5.12 (FORCEON), U5.15 (VCC), U5.16 (~FORCEOFF), U6.5 (VDDIO), U6.8 (VDD), U6.12 (AP_CS); also elsewhere on the board
+5V: L2.2, R11.1, U4.VIN; also elsewhere on the board
+12V: C1.1, J1.2, L1.1; also elsewhere on the board
/DEBUG_UART_RX: J6.2, U4.0 (0/RX1/CRX2/PWM)
/DEBUG_UART_TX: J6.3, U4.1 (1/TX1/CTX2)
/Dynamixel/DYNAMIXEL_ENABLE: U4.2 (2/OUT2/PWM); also elsewhere on the board
/Dynamixel/DYNAMIXEL_TTL_DIR: U4.9 (9/OUT1C/PWM); also elsewhere on the board
/Dynamixel/DYNAMIXEL_TTL_RX: U4.7 (7/RX2/OUT1A/PWM); also elsewhere on the board
/Dynamixel/DYNAMIXEL_TTL_TX: U4.8 (8/TX2/IN1/PWM); also elsewhere on the board
/I2C_SCL: R7.2, U4.19 (19/A5/SCL0/PWM), U6.13 (AP_SCL/AP_SCLK)
/I2C_SDA: R8.2, U4.18 (18/A4/SDA0/PWM), U6.14 (AP_SDA/AP_SDIO/AP_SDI)
/IMU_INT1: U4.14 (14/A0/TX3/SPDIF_OUT/PWM), U6.4 (INT1/INT)
/IMU_INT2: U4.15 (15/A1/RX3/SPDIF_IN/PWM), U6.9 (INT2/FSYNC)
/LIMIT_SWITCH: U2.4 (Y), U4.22 (22/A8/CTX1/PWM)
/UART_RX: U4.21 (21/A7/RX5/BCLK1), U5.9 (ROUT)
/UART_TX: U4.20 (20/A6/TX5/LRCLK1), U5.11 (DIN)
/~RS232_INVALID: U4.23 (23/A9/CRX1/MCLK1/PWM), U5.10 (~INVALID)
GND: C1.2, C2.2, C3.2, C4.2, C5.2, C6.2, C7.2, C10.2, C11.2, C12.2, C13.2, C14.2, J1.1, J2.1, J6.1, R10.2, SW1.1 (A), U1.2 (GND), U2.3 (GND), U4.GND_1 (GND), U5.1 (~EN), U5.14 (GND), U6.6 (GND); also elsewhere on the board
unnamed: C2.1, L1.2, U1.1 (VIN)
unnamed: C3.1, R4.2
unnamed: C5.1, R3.2, U2.2 (A)
unnamed: C8.1, U5.2 (C1+)
unnamed: C8.2, U5.4 (C1-)
unnamed: C9.1, U5.5 (C2+)
unnamed: C9.2, U5.6 (C2-)
unnamed: C10.1, U5.3 (V+)
unnamed: C11.1, U5.7 (V-)
unnamed: C14.1, R11.2
unnamed: J2.2, U5.8 (RIN)
unnamed: J2.3, U5.13 (DOUT)
unnamed: L2.1, R4.1, U1.3 (VOUT)
unnamed: R1.2, R3.1, SW1.2 (B)
unnamed: R9.2, R10.1, U6.1 (AP_SDO/AP_AD0)

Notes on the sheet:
SW1: JST PH Connector
J2: JST PH Connector
RS232
Limit Switch
J6: Wires
IMU
J1: T-Connector
Debug UART
Power
MCU
I2C Address 1101000: R9=NI, R10=0 1101001: R9=0, R10=NI NI: Not Installed

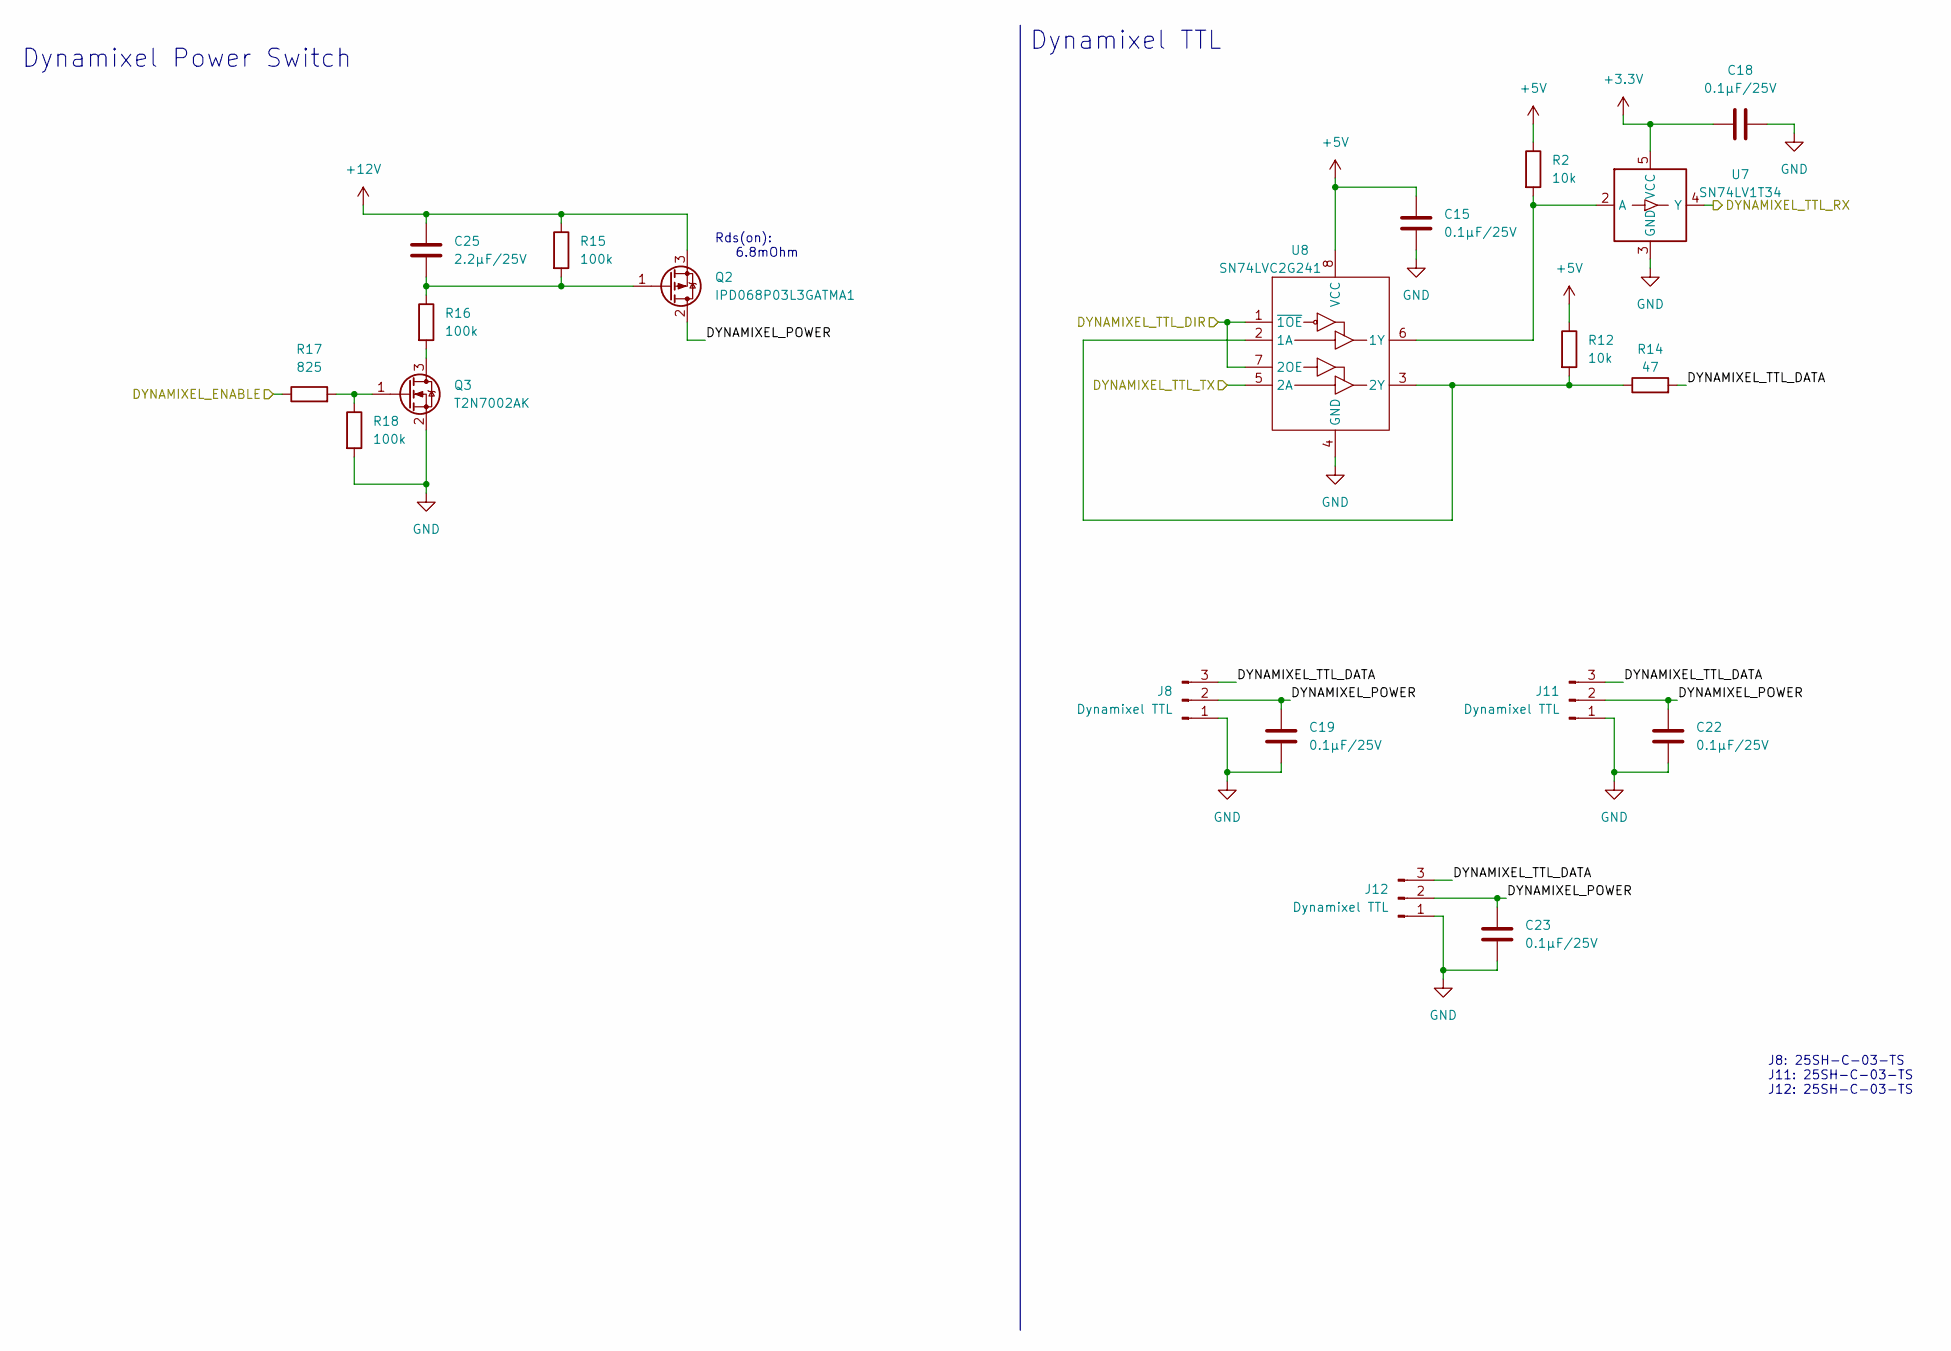
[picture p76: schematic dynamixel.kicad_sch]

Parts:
C15, C18, C19, C22, C23: 0.1µF/25V; C_0805_2012Metric
C25: 2.2µF/25V; C_0805_2012Metric
J8, J11, J12: Dynamixel TTL; 25SH-C-03-TS
Q2: IPD068P03L3GATMA1; TO-252-2
Q3: T2N7002AK; SOT-23
R2, R12: 10k; R_0805_2012Metric
R14: 47; R_0805_2012Metric
R15, R16, R18: 100k; R_0805_2012Metric
R17: 825; R_0805_2012Metric
U7: SN74LV1T34; SOT-23-5
U8: SN74LVC2G241; VSSOP-8_2.3x2mm_P0.5mm

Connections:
+3.3V: C18.1, U7.5 (VCC); also elsewhere on the board
+5V: C15.1, R2.1, R12.1, U8.8 (VCC); also elsewhere on the board
+12V: C25.1, Q2.3 (S), R15.1; also elsewhere on the board
/Dynamixel/DYNAMIXEL_ENABLE: R17.1; also elsewhere on the board
/Dynamixel/DYNAMIXEL_POWER: C19.1, C22.1, C23.1, J8.2, J11.2, J12.2, Q2.2 (D)
/Dynamixel/DYNAMIXEL_TTL_DATA: J8.3, J11.3, J12.3, R14.2
/Dynamixel/DYNAMIXEL_TTL_DIR: U8.1 (~1OE), U8.7 (2OE); also elsewhere on the board
/Dynamixel/DYNAMIXEL_TTL_RX: U7.4 (Y); also elsewhere on the board
/Dynamixel/DYNAMIXEL_TTL_TX: U8.5 (2A); also elsewhere on the board
GND: C15.2, C18.2, C19.2, C22.2, C23.2, J8.1, J11.1, J12.1, Q3.2 (S), R18.2, U7.3 (GND), U8.4 (GND); also elsewhere on the board
unnamed: C25.2, Q2.1 (G), R15.2, R16.1
unnamed: Q3.1 (G), R17.2, R18.1
unnamed: Q3.3 (D), R16.2
unnamed: R2.2, U7.2 (A), U8.6 (1Y)
unnamed: R12.2, R14.1, U8.2 (1A), U8.3 (2Y)

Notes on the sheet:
J8: 25SH-C-03-TS J11: 25SH-C-03-TS J12: 25SH-C-03-TS
Rds(on): 6.8mOhm
Dynamixel Power Switch
Dynamixel TTL



Board: 4 copper layers, 36.0 x 56.0 mm, 54 parts (16 on the bottom side), 40 nets.

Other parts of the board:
MH1: MountingHole_3.2mm_M3

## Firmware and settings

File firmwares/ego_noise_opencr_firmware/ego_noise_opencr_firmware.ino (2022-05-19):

#include <Arduino.h>

#include <ros.h>
#include <std_msgs/Int32.h>
#include <std_msgs/Int32MultiArray.h>
#include <std_msgs/Float32.h>
#include <std_msgs/Empty.h>

#include "IoMapping.h"
#include "TorsoController.h"
#include "ServoSpeedController.h"

#include <cmath>

// Constants
constexpr unsigned long INIT_DELAY_MS = 10000;
constexpr unsigned long DATA_GATHERING_DELAY_MS = 500;
constexpr unsigned long AUDIO_RECORDING_DELAY_MS = 1000;
constexpr unsigned long TORSO_STEP_DELAY_MS = 10;

constexpr float HEAD_SERVO_TORSO_ORIENTATION_START = 0;
constexpr float HEAD_SERVO_TORSO_ORIENTATION_END = 2 * M_PI;
constexpr float HEAD_SERVO_TORSO_ORIENTATION_STEP = HEAD_SERVO_TORSO_ORIENTATION_END / 36;

constexpr int32_t HEAD_SERVO_SPEED_START = 20;
constexpr int32_t HEAD_SERVO_SPEED_END = 265;
constexpr int32_t HEAD_SERVO_SPEED_STEP = 5;

constexpr int32_t TORSO_SERVO_SPEED_START = 20;
constexpr int32_t TORSO_SERVO_SPEED_END = TORSO_MAX_VELOCITY;
constexpr int32_t TORSO_SERVO_SPEED_STEP = 5;

constexpr float TORSO_SERVO_TORSO_ORIENTATION_START = M_PI / 2;
constexpr float TORSO_SERVO_TORSO_ORIENTATION_END = 4 * M_PI + M_PI / 2;

// ROS
constexpr unsigned long ROS_SERIAL_BAUD_RATE = 1000000;
static ros::NodeHandle nh;

static std_msgs::Float32 currentTorsoOrientationMsg;
static ros::Publisher currentTorsoOrientationPub("opencr/current_torso_orientation", &currentTorsoOrientationMsg);

static std_msgs::Int32 movingServoIdMsg;
static ros::Publisher movingServoIdPub("opencr/moving_servo_id", &movingServoIdMsg);

static std_msgs::Int32 movingServoSpeedTargetMsg;
static ros::Publisher movingServoSpeedTargetPub("opencr/moving_servo_speed_target", &movingServoSpeedTargetMsg);

static std_msgs::Int32 movingServoSpeedMsg;
static ros::Publisher movingServoSpeedPub("opencr/moving_servo_speed", &movingServoSpeedMsg);

static std_msgs::Empty startHeadServoAudioRecordingMsg;
static ros::Publisher
    startHeadServoAudioRecordingPub("opencr/start_head_servo_audio_recording", &startHeadServoAudioRecordingMsg);

static std_msgs::Empty stopHeadServoAudioRecordingMsg;
static ros::Publisher
    stopHeadServoAudioRecordingPub("opencr/stop_head_servo_audio_recording", &stopHeadServoAudioRecordingMsg);

static std_msgs::Empty startTorsoServoAudioRecordingMsg;
static ros::Publisher
    startTorsoServoAudioRecordingPub("opencr/start_torso_servo_audio_recording", &startTorsoServoAudioRecordingMsg);

static std_msgs::Empty stopTorsoServoAudioRecordingMsg;
static ros::Publisher
    stopTorsoServoAudioRecordingPub("opencr/stop_torso_servo_audio_recording", &stopTorsoServoAudioRecordingMsg);

static void startEgoNoiseDataGathering(const std_msgs::Empty& msg);
static ros::Subscriber<std_msgs::Empty>
    startEgoNoiseDataGatheringSub("opencr/start_ego_noise_data_gathering", &startEgoNoiseDataGathering);

const char* DYNAMIXEL_BUS_SERIAL = "/dev/ttyUSB0";
constexpr long DYNAMIXEL_BAUDRATE = 1000000;
DynamixelWorkbench dynamixelWorkbench;

static bool dataGatheringStarted = false;

static void gatherEgoNoiseData();

void setup()
{
    nh.getHardware()->setBaud(ROS_SERIAL_BAUD_RATE);

    nh.initNode();
    nh.subscribe(startEgoNoiseDataGatheringSub);

    nh.advertise(currentTorsoOrientationPub);
    nh.advertise(movingServoIdPub);
    nh.advertise(movingServoSpeedTargetPub);
    nh.advertise(movingServoSpeedPub);
    nh.advertise(startHeadServoAudioRecordingPub);
    nh.advertise(stopHeadServoAudioRecordingPub);
    nh.advertise(startTorsoServoAudioRecordingPub);
    nh.advertise(stopTorsoServoAudioRecordingPub);

    dynamixelWorkbench.begin(DYNAMIXEL_BUS_SERIAL, DYNAMIXEL_BAUDRATE);
}

void loop()
{
    if (!dataGatheringStarted)
    {
        nh.spinOnce();
    }
    else
    {
        gatherEgoNoiseData();
        dataGatheringStarted = false;
    }
}

void nhDelay(unsigned long ms)
{
    unsigned long start = millis();

    while ((millis() - start) < ms)
    {
        nh.spinOnce();
    }
}

static void startEgoNoiseDataGathering(const std_msgs::Empty& msg)
{
    dataGatheringStarted = true;
}

static void sendTorsoOrientation(TorsoController& torsoController)
{
    currentTorsoOrientationMsg.data = torsoController.readOrientation();
    currentTorsoOrientationPub.publish(&currentTorsoOrientationMsg);
}

static void sendTorsoOrientation(float orientation)
{
    currentTorsoOrientationMsg.data = orientation;
    currentTorsoOrientationPub.publish(&currentTorsoOrientationMsg);
}

static void sendMovingServoId(uint8_t id)
{
    movingServoIdMsg.data = id;
    movingServoIdPub.publish(&movingServoIdMsg);
}

static void sendMovingServoSpeedTarget(int32_t speed)
{
    movingServoSpeedTargetMsg.data = speed;
    movingServoSpeedTargetPub.publish(&movingServoSpeedTargetMsg);
}

static void sendMovingServoSpeed(int32_t speed)
{
    movingServoSpeedMsg.data = speed;
    movingServoSpeedPub.publish(&movingServoSpeedMsg);
}

static void startHeadServoAudioRecording()
{
    startHeadServoAudioRecordingPub.publish(&startHeadServoAudioRecordingMsg);
}

static void stopHeadServoAudioRecording()
{
    stopHeadServoAudioRecordingPub.publish(&stopHeadServoAudioRecordingMsg);
}

static void startTorsoServoAudioRecording()
{
    startTorsoServoAudioRecordingPub.publish(&startTorsoServoAudioRecordingMsg);
}

static void stopTorsoServoAudioRecording()
{
    stopTorsoServoAudioRecordingPub.publish(&stopTorsoServoAudioRecordingMsg);
}

static void gatherHeadServoEgoNoiseData()
{
    ServoSpeedController servoSpeedControllers[STEWART_SERVO_COUNT] = {
        ServoSpeedController(dynamixelWorkbench, STEWART_PLATFORM_DYNAMIXEL_IDS[0]),
        ServoSpeedController(dynamixelWorkbench, STEWART_PLATFORM_DYNAMIXEL_IDS[1]),
        ServoSpeedController(dynamixelWorkbench, STEWART_PLATFORM_DYNAMIXEL_IDS[2]),
        ServoSpeedController(dynamixelWorkbench, STEWART_PLATFORM_DYNAMIXEL_IDS[3]),
        ServoSpeedController(dynamixelWorkbench, STEWART_PLATFORM_DYNAMIXEL_IDS[4]),
        ServoSpeedController(dynamixelWorkbench, STEWART_PLATFORM_DYNAMIXEL_IDS[5])};

    for (size_t servoIndex = 0; servoIndex < STEWART_SERVO_COUNT; servoIndex++)
    {
        sendMovingServoId(STEWART_PLATFORM_DYNAMIXEL_IDS[servoIndex]);

        for (int32_t speed = HEAD_SERVO_SPEED_START; speed <= HEAD_SERVO_SPEED_END; speed += HEAD_SERVO_SPEED_STEP)
        {
            sendMovingServoSpeedTarget(speed);
            servoSpeedControllers[servoIndex].setSpeed(speed);
            nhDelay(DATA_GATHERING_DELAY_MS);
            sendMovingServoSpeed(servoSpeedControllers[servoIndex].readSpeed());
            nhDelay(DATA_GATHERING_DELAY_MS);

            startHeadServoAudioRecording();
            nhDelay(AUDIO_RECORDING_DELAY_MS);
            stopHeadServoAudioRecording();
        }

        servoSpeedControllers[servoIndex].setSpeed(0);
    }
}

static void gatherAllHeadServoEgoNoiseData()
{
    TorsoController torsoController(dynamixelWorkbench);
    torsoController.init();
    nhDelay(INIT_DELAY_MS);

    for (float o = HEAD_SERVO_TORSO_ORIENTATION_START; o < HEAD_SERVO_TORSO_ORIENTATION_END;
         o += HEAD_SERVO_TORSO_ORIENTATION_STEP)
    {
        torsoController.setOrientation(o);
        nhDelay(DATA_GATHERING_DELAY_MS);
        sendTorsoOrientation(torsoController);
        nhDelay(DATA_GATHERING_DELAY_MS);

        gatherHeadServoEgoNoiseData();
    }
    torsoController.setOrientation(0);
    nhDelay(INIT_DELAY_MS);
}

static void gatherTorsoServoEgoNoiseData(int32_t speed)
{
    sendMovingServoSpeedTarget(speed);
    {
        TorsoController torsoController(dynamixelWorkbench);
        torsoController.init();
        nhDelay(INIT_DELAY_MS);
    }

    ServoSpeedController servoSpeedController(dynamixelWorkbench, TORSO_DYNAMIXEL_ID);

    float lastPosition = fmodRadian(servoSpeedController.readPosition());
    float orientation = 0.f;
    bool recordingStarted = false;

    sendMovingServoSpeedTarget(speed);
    servoSpeedController.setSpeed(speed);

    while (orientation < TORSO_SERVO_TORSO_ORIENTATION_END)
    {
        if (orientation > TORSO_SERVO_TORSO_ORIENTATION_START && !recordingStarted)
        {
            startTorsoServoAudioRecording();
            recordingStarted = true;
        }

        float position = fmodRadian(servoSpeedController.readPosition());
        orientation += fmodRadian(position - lastPosition) * TORSO_GEAR_RATIO;
        lastPosition = position;

        sendTorsoOrientation(fmodRadian(orientation));
        sendMovingServoSpeed(servoSpeedController.readSpeed());
        nhDelay(TORSO_STEP_DELAY_MS);
    }

    stopTorsoServoAudioRecording();
    nhDelay(DATA_GATHERING_DELAY_MS);
}

static void gatherAllTorsoServoEgoNoiseData()
{
    sendMovingServoId(TORSO_DYNAMIXEL_ID);
    nhDelay(DATA_GATHERING_DELAY_MS);

    for (int32_t speed = TORSO_SERVO_SPEED_START; speed <= TORSO_SERVO_SPEED_END; speed += TORSO_SERVO_SPEED_STEP)
    {
        gatherTorsoServoEgoNoiseData(speed);
    }
}

static void gatherEgoNoiseData()
{
    gatherAllHeadServoEgoNoiseData();
    gatherAllTorsoServoEgoNoiseData();
}

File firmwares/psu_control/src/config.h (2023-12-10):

#ifndef PSU_CONTROL_CONFIG_H
#define PSU_CONTROL_CONFIG_H

#include <cstdint>
#include <cstddef>

// Firmware configuration
#define FIRMWARE_MODE_SETUP_BATTERY_CHARGER 1
#define FIRMWARE_MODE_NORMAL                2
#define FIRMWARE_MODE_PCB_TEST              3
#define FIRMWARE_MODE_COMMUNICATION_TEST    4
#define FIRMWARE_MODE                       FIRMWARE_MODE_NORMAL

// Device configuration
#define DEBUG_SERIAL Serial
constexpr long DEBUG_SERIAL_BAUD_RATE = 250000;

constexpr uint32_t WIRE_CLOCK = 100000;

constexpr uint32_t PWM_RESOLUTION = 12;
constexpr float PWM_MAX_VALUE = 4095.f;

constexpr uint32_t ADC_RESOLUTION = 12;
constexpr float ADC_MAX_VALUE = 4095.f;

constexpr uint8_t POWER_OFF_PIN = 2;
constexpr uint8_t POWER_SWITCH_PIN = 12;
constexpr uint32_t SHUTDOWN_REQUEST_TIMEOUT_MS = 120000;
constexpr float SHUTDOWN_COMPLETED_FOR_COMPUTER_AND_DYNAMIXELS_POWER_THRESHOLD_W = 7.5f;

#define BATTERY_WIRE Wire
constexpr uint8_t BATTERY_STATUS_PIN = 20;
constexpr uint8_t CHARGER_STATUS_PIN = 21;
constexpr float BATTERY_CHARGER_CHARGE_CURRENT_LIMIT = 1.f;
constexpr float BATTERY_CHARGER_INPUT_CURRENT_LIMIT = 9.47f;

constexpr uint8_t LED_STRIP_PIN = 1;
constexpr size_t STATE_OF_CHARGE_LED_COUNT = 5;
constexpr size_t VOLUME_LED_COUNT = 5;
constexpr size_t BASE_LED_COUNT = 28;
constexpr size_t LED_COUNT = STATE_OF_CHARGE_LED_COUNT + VOLUME_LED_COUNT + BASE_LED_COUNT;
constexpr uint8_t LED_STRIP_MINIMUM_BRIGHTNESS = 64;
constexpr uint8_t LED_STRIP_MAXIMUM_BRIGHTNESS = 128;

constexpr uint8_t FAN_PIN = 3;
constexpr float FAN_PWM_FREQUENCY = 46875;
constexpr float FAN_HYSTERESIS = 1;
constexpr float FAN_TEMPERATURE_STEP_1 = 40;
constexpr float FAN_TEMPERATURE_STEP_2 = 60;

constexpr uint8_t BUZZER_PIN = 6;
constexpr float BUZZER_PWM_FREQUENCY = 2400;
constexpr uint32_t BUZZER_ON_OFF_INTERVAL_US = 1000000;
constexpr float BUZZER_STATE_OF_CHARGE_LIMIT = 5;

#define AUDIO_POWER_AMPLIFIER_WIRE Wire1
constexpr size_t AUDIO_POWER_AMPLIFIER_COUNT = 2;
constexpr uint8_t AUDIO_POWER_AMPLIFIER_I2C_ADDRESSES[AUDIO_POWER_AMPLIFIER_COUNT] = {0x4a, 0x4b};
constexpr uint8_t AUDIO_POWER_AMPLIFIER_DEFAULT_VOLUME = 24;
constexpr uint8_t AUDIO_POWER_AMPLIFIER_BATTERY_MAXIMUM_VOLUME = 45;
constexpr uint8_t AUDIO_POWER_AMPLIFIER_MAXIMUM_VOLUME = 63;

#define CURRENT_VOLTAGE_SENSOR_WIRE Wire1
constexpr uint8_t CURRENT_VOLTAGE_SENSOR_ADDRESS = 0x40;
constexpr float CURRENT_VOLTAGE_SENSOR_SHUNT_RESISTOR = 0.004f;
constexpr uint8_t CURRENT_VOLTAGE_SENSOR_MAX_CURRENT = 10;

constexpr uint8_t ONBOARD_TEMPERATURE_PIN = 14;
constexpr float ONBOARD_TEMPERATURE_NTC_R = 10000;  // @ 25°C
constexpr float ONBOARD_TEMPERATURE_NTC_BETA = 3940;
constexpr float ONBOARD_TEMPERATURE_R = 10000;
constexpr uint8_t EXTERNAL_TEMPERATURE_PIN = 15;
constexpr float EXTERNAL_TEMPERATURE_NTC_R = 10000;  // @ 25°C
constexpr float EXTERNAL_TEMPERATURE_NTC_BETA = 3936;
constexpr float EXTERNAL_TEMPERATURE_R = 10000;

constexpr uint8_t FRONT_LIGHT_SENSOR_PIN = 16;
constexpr uint8_t BACK_LIGHT_SENSOR_PIN = 25;
constexpr uint8_t LEFT_LIGHT_SENSOR_PIN = 17;
constexpr uint8_t RIGHT_LIGHT_SENSOR_PIN = 24;
constexpr float LIGHT_SENSOR_MINIMUM_VALUE = ADC_MAX_VALUE * 0.0f;
constexpr float LIGHT_SENSOR_MAXIMUM_VALUE = ADC_MAX_VALUE * 0.03f;

constexpr uint8_t START_BUTTON_PIN = 11;
constexpr uint8_t STOP_BUTTON_PIN = 10;
constexpr uint8_t VOLUME_UP_BUTTON_PIN = 9;
constexpr uint8_t VOLUME_DOWN_BUTTON_PIN = 4;
constexpr uint32_t VOLUME_BUTTON_INTERVAL_MS = 250;

// Communication configuration
#define COMMUNICATION_SERIAL Serial3
constexpr uint8_t COMMUNICATION_RS232_INVALID = 5;
constexpr long COMMUNICATION_SERIAL_BAUD_RATE = 250000;
constexpr uint32_t COMMUNICATION_ACKNOWLEDGMENT_TIMEOUT_MS = 100;
constexpr uint32_t COMMUNICATION_MAXIMUM_TRIAL_COUNT = 5;

// Timing configuration
constexpr uint32_t ERROR_DELAY_MS = 1000;
constexpr uint32_t STATUS_TICKER_INTERVAL_MS = 250;
constexpr uint32_t BUTTON_TICKER_INTERVAL_MS = 100;
constexpr uint32_t SHUTDOWN_PENDING_DELAY_MS = 1000;

#endif

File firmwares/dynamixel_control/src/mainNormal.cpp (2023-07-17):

#include "config.h"

#if FIRMWARE_MODE == FIRMWARE_MODE_NORMAL

#include "criticalError.h"
#include "mainCommon.h"
#include "actuators/StewartPlatformController.h"
#include "actuators/TorsoController.h"

#include <SerialCommunication.h>

#include <Ticker.h>

static TeensySerialPort<decltype(COMPUTER_COMMUNICATION_SERIAL)>
    computerSerialCommunicationSerialPort(COMPUTER_COMMUNICATION_SERIAL);
static SerialCommunicationManager computerSerialCommunicationManager(
    Device::DYNAMIXEL_CONTROL,
    COMMUNICATION_ACKNOWLEDGMENT_TIMEOUT_MS,
    COMMUNICATION_MAXIMUM_TRIAL_COUNT,
    computerSerialCommunicationSerialPort);

static TeensySerialPort<decltype(PSU_CONTROL_COMMUNICATION_SERIAL)>
    psuControlSerialCommunicationSerialPort(PSU_CONTROL_COMMUNICATION_SERIAL);
static SerialCommunicationManager psuControlSerialCommunicationManager(
    Device::DYNAMIXEL_CONTROL,
    COMMUNICATION_ACKNOWLEDGMENT_TIMEOUT_MS,
    COMMUNICATION_MAXIMUM_TRIAL_COUNT,
    psuControlSerialCommunicationSerialPort);

static volatile bool imuDataReady = false;

static StewartPlatformController stewartPlatformController(dynamixel);
static TorsoController torsoController(dynamixel);

static void setupSerialCommunicationManagers();
static void setupControllers();

static void onMotorStatusTicker();
static void onImuDataReadyInterrupt();
static void sendImuData();

static void onSetHeadPoseMessage(Device source, const SetHeadPosePayload& payload);
static void onSetTorsoOrientationMessage(Device source, const SetTorsoOrientationPayload& payload);
static void onShutdownMessage(Device source, const ShutdownPayload& payload);
static void computerRouteCallback(Device destination, const uint8_t* data, size_t size);
static void psuControlRouteCallback(Device destination, const uint8_t* data, size_t size);
static void logInvalidRoute(const char* device, Device destination);
static void onComputerSerialCommunicationError(const char* message, tl::optional<MessageType> messageType);
static void onPsuControlSerialCommunicationError(const char* message, tl::optional<MessageType> messageType);
static void onSerialCommunicationError(const char* message, tl::optional<MessageType> messageType);

Ticker motorStatusTicker(onMotorStatusTicker, MOTOR_STATUS_TICKER_INTERVAL_MS, 0, MILLIS);

void setup()
{
    // put your setup code here, to run once:
    setupDebugSerial();
    setupWire();

    imuDataReady = false;
    setupImu(onImuDataReadyInterrupt);
    setupSerialCommunicationManagers();
    setupDynamixel();
    setupControllers();

    motorStatusTicker.start();
}

static void setupSerialCommunicationManagers()
{
    DEBUG_SERIAL.println("Setup Serial Communication Manager - Start");

    COMPUTER_COMMUNICATION_SERIAL.begin(COMMUNICATION_SERIAL_BAUD_RATE);
    computerSerialCommunicationManager.setSetHeadPoseHandler(onSetHeadPoseMessage);
    computerSerialCommunicationManager.setSetTorsoOrientationHandler(onSetTorsoOrientationMessage);
    computerSerialCommunicationManager.setRouteCallback(computerRouteCallback);
    computerSerialCommunicationManager.setErrorCallback(onComputerSerialCommunicationError);

    pinMode(PSU_CONTROL_COMMUNICATION_RS232_INVALID, INPUT);
    PSU_CONTROL_COMMUNICATION_SERIAL.begin(COMMUNICATION_SERIAL_BAUD_RATE);
    psuControlSerialCommunicationManager.setShutdownHandler(onShutdownMessage);
    psuControlSerialCommunicationManager.setRouteCallback(psuControlRouteCallback);
    psuControlSerialCommunicationManager.setErrorCallback(onPsuControlSerialCommunicationError);

    DEBUG_SERIAL.println("Setup Serial Communication Manager - End");
}

static void setupControllers()
{
    DEBUG_SERIAL.println("Setup Controllers - Start");

    if (!stewartPlatformController.begin())
    {
        CRITICAL_ERROR("stewartPlatformController.begin() failed");
    }

    torsoController.begin();

    DEBUG_SERIAL.println("Setup Controllers - End");
}

void loop()
{
    if (imuDataReady)
    {
        imuDataReady = false;
        sendImuData();
    }

    motorStatusTicker.update();

    computerSerialCommunicationManager.update(millis());
    psuControlSerialCommunicationManager.update(millis());
}

static void onMotorStatusTicker()
{
    MotorStatusPayload motorStatusPayload;
    motorStatusPayload.torsoOrientation = torsoController.readOrientation();
    motorStatusPayload.torsoServoSpeed = torsoController.readServoSpeed();

    float headServoAngles[STEWART_SERVO_COUNT];
    HeadPose headPose;
    int16_t headServoSpeeds[STEWART_SERVO_COUNT];
    stewartPlatformController.readCurrentPose(headServoAngles, headPose);
    stewartPlatformController.readServoSpeeds(headServoSpeeds);

    motorStatusPayload.headServoAngle1 = headServoAngles[0];
    motorStatusPayload.headServoAngle2 = headServoAngles[1];
    motorStatusPayload.headServoAngle3 = headServoAngles[2];
    motorStatusPayload.headServoAngle4 = headServoAngles[3];
    motorStatusPayload.headServoAngle5 = headServoAngles[4];
    motorStatusPayload.headServoAngle6 = headServoAngles[5];
    motorStatusPayload.headServoSpeed1 = headServoSpeeds[0];
    motorStatusPayload.headServoSpeed2 = headServoSpeeds[1];
    motorStatusPayload.headServoSpeed3 = headServoSpeeds[2];
    motorStatusPayload.headServoSpeed4 = headServoSpeeds[3];
    motorStatusPayload.headServoSpeed5 = headServoSpeeds[4];
    motorStatusPayload.headServoSpeed6 = headServoSpeeds[5];
    motorStatusPayload.headPosePositionX = headPose.positionX;
    motorStatusPayload.headPosePositionY = headPose.positionY;
    motorStatusPayload.headPosePositionZ = headPose.positionZ;
    motorStatusPayload.headPoseOrientationW = headPose.orientationW;
    motorStatusPayload.headPoseOrientationX = headPose.orientationX;
    motorStatusPayload.headPoseOrientationY = headPose.orientationY;
    motorStatusPayload.headPoseOrientationZ = headPose.orientationZ;
    motorStatusPayload.isHeadPoseReachable = stewartPlatformController.isPoseReachable();

    computerSerialCommunicationManager.send(Device::COMPUTER, motorStatusPayload, millis());
}

static void onImuDataReadyInterrupt()
{
    imuDataReady = true;
}

static void sendImuData()
{
    if (!imu.readData())
    {
        return;
    }

    ImuDataPayload imuDataPayload;
    imuDataPayload.accelerationX = imu.getAccelerationXInMPerSS();
    imuDataPayload.accelerationY = imu.getAccelerationYInMPerSS();
    imuDataPayload.accelerationZ = imu.getAccelerationZInMPerSS();
    imuDataPayload.angularRateX = imu.getAngularRateXInRadPerS();
    imuDataPayload.angularRateY = imu.getAngularRateYInRadPerS();
    imuDataPayload.angularRateZ = imu.getAngularRateZInRadPerS();

    computerSerialCommunicationManager.send(Device::COMPUTER, imuDataPayload, millis());
}
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

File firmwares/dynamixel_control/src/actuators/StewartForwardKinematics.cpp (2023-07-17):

#include "StewartForwardKinematics.h"

#include <cmath>

StewartForwardKinematics::StewartForwardKinematics() : m_solver(TrustRegionReflectiveParameters()) {}

void StewartForwardKinematics::calculatePose(
    Eigen::Vector3f& position,
    Eigen::Quaternionf& orientation,
    const Eigen::Matrix<float, 6, 1>& servoAngles)
{
    calculateBottomAnchors(servoAngles);

    auto func = [this](
                    Eigen::Matrix<float, SOLVER_X_SIZE, 1>& f,
                    Eigen::Matrix<float, SOLVER_X_SIZE, SOLVER_X_SIZE>& J,
                    const Eigen::Matrix<float, SOLVER_X_SIZE, 1>& x) { solverFunction(f, J, x); };

    TrustRegionReflectiveSolverResult<SOLVER_X_SIZE> result = m_solver.solve(
        func,
        STEWART_FORWARD_KINEMATICS_X0,
        STEWART_FORWARD_KINEMATICS_MIN_BOUNDS,
        STEWART_FORWARD_KINEMATICS_MAX_BOUNDS);

    position.x() = result.x[0];
    position.y() = result.x[1];
    position.z() = result.x[2];

    orientation = Eigen::AngleAxisf(result.x[3], Eigen::Vector3f::UnitX()) *
                  Eigen::AngleAxisf(result.x[4], Eigen::Vector3f::UnitY()) *
                  Eigen::AngleAxisf(result.x[5], Eigen::Vector3f::UnitZ());
}

void StewartForwardKinematics::calculateBottomAnchors(const Eigen::Matrix<float, STEWART_SERVO_COUNT, 1>& servoAngles)
{
    for (size_t i = 0; i < STEWART_SERVO_COUNT; i++)
    {
        float servoAngle = servoAngles[i];
        if (STEWART_IS_HORN_ORIENTATION_REVERSED[i])
        {
            servoAngle = -servoAngle;
        }

        float cosServoAngle = std::cos(servoAngle);
        m_bottomAnchors[i].x() = STEWART_BOTTOM_LINEAR_ACTUATOR_ANCHORS[i].x() +
                                 STEWART_HORN_LENGTH * cosServoAngle * std::cos(STEWART_HORN_ORIENTATION_ANGLES[i]);
        m_bottomAnchors[i].y() = STEWART_BOTTOM_LINEAR_ACTUATOR_ANCHORS[i].y() +
                                 STEWART_HORN_LENGTH * cosServoAngle * std::sin(STEWART_HORN_ORIENTATION_ANGLES[i]);
        m_bottomAnchors[i].z() =
            STEWART_BOTTOM_LINEAR_ACTUATOR_ANCHORS[i].z() + STEWART_HORN_LENGTH * std::sin(servoAngle);
    }
}

void StewartForwardKinematics::solverFunction(
    Eigen::Matrix<float, SOLVER_X_SIZE, 1>& f,
    Eigen::Matrix<float, SOLVER_X_SIZE, SOLVER_X_SIZE>& J,
    const Eigen::Matrix<float, SOLVER_X_SIZE, 1>& x)
{
    for (int i = 0; i < SOLVER_X_SIZE; i++)
    {
        float error;
        Eigen::Matrix<float, SOLVER_X_SIZE, 1> grad;
        calculateRodLengthErrorAndGrad(
            error,
            grad,
            m_bottomAnchors[i].x(),
            m_bottomAnchors[i].y(),
            m_bottomAnchors[i].z(),
            STEWART_TOP_ANCHORS[i].x(),
            STEWART_TOP_ANCHORS[i].y(),
            STEWART_TOP_ANCHORS[i].z(),
            x[0],
            x[1],
            x[2],
            x[3],
            x[4],
            x[5],
            STEWART_ROD_LENGTH);

        f[i] = error;
        J.row(i) = grad.transpose();
    }
}

void StewartForwardKinematics::calculateRodLengthErrorAndGrad(
    float& error,
    Eigen::Matrix<float, SOLVER_X_SIZE, 1>& grad,
    float bax,
    float bay,
    float baz,
    float itax,
    float itay,
    float itaz,
    float tx,
    float ty,
    float tz,
    float rx,
    float ry,
    float rz,
    float d)
{
    float sinRx = std::sin(rx);
    float cosRx = std::cos(rx);
    float sinRy = std::sin(ry);
    float cosRy = std::cos(ry);
    float sinRz = std::sin(rz);
    float cosRz = std::cos(rz);

    float cosRyCosRz = cosRy * cosRz;
    float sinRzCosRy = sinRz * cosRy;
    float sin_rx_sin_ry_cos_rz = sinRx * sinRy * cosRz;
    float sinRzCosRx = sinRz * cosRx;
    float sinRxSinRySinRz = sinRx * sinRy * sinRz;
    float cosRxCosRz = cosRx * cosRz;
    float sinRxCosRy = sinRx * cosRy;
    float sinRxSinRz = sinRx * sinRz;
    float sinRxCosRyCosRz = sinRx * cosRyCosRz;
    float sinRyCosRxCosRz = sinRy * cosRxCosRz;
    float sinRxCosRz = sinRx * cosRz;
    float sinRxSinRzCosRy = sinRx * sinRzCosRy;
    float sinRySinRzCosRx = sinRy * sinRzCosRx;
    float cosRxCosRy = cosRx * cosRy;
    float sinRzCosRxCosRy = sinRzCosRx * cosRy;
    float cosRxCosRyCosRz = cosRxCosRy * cosRz;
    float sinRyCosRz = sinRy * cosRz;
    float sinRySinRz = sinRy * sinRz;
    float sinRyCosRx = sinRy * cosRx;
    float sinRxSinRy = sinRx * sinRy;

    float denominator = std::sqrt(
        std::pow(-bax + itax * cosRyCosRz - itay * sinRzCosRy + itaz * sinRy + tx, 2.f) +
        std::pow(
            -bay + itax * (sin_rx_sin_ry_cos_rz + sinRzCosRx) - itay * (sinRxSinRySinRz - cosRxCosRz) -
                itaz * sinRxCosRy + ty,
            2.f) +
        std::pow(
            -baz + itax * (sinRxSinRz - sinRyCosRxCosRz) + itay * (sinRxCosRz + sinRySinRzCosRx) + itaz * cosRxCosRy +
                tz,
            2.f));

    error = -d + denominator;

    grad[0] = (-bax + itax * cosRyCosRz - itay * sinRzCosRy + itaz * sinRy + tx) / denominator;
    grad[1] = (-bay + itax * (sin_rx_sin_ry_cos_rz + sinRzCosRx) - itay * (sinRxSinRySinRz - cosRxCosRz) -
               itaz * sinRxCosRy + ty) /
              denominator;
    grad[2] = (-baz + itax * (sinRxSinRz - sinRyCosRxCosRz) + itay * (sinRxCosRz + sinRySinRzCosRx) +
               itaz * cosRxCosRy + tz) /
              denominator;
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

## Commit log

2021-12-16 Doc (#1)
    * Add BOMs
    * Rename link to Link
    * Add images. Add Dynamixel configuration steps.
    * Fixes
    * Fix doc
    * Add cable assembly instructions. Add PCB assembly instructions.
    * Complete BOM
    * Add the Buck-Boost PCB BOM. Add PCB assembly steps. Fix mistakes.
    * Add assembly steps
    * Add CAD files.
    * Add robot.STEP
    * stewart simulator
    * Add odas configuration generators
    * Add dance movement generators.
    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
    [36-24337-ND.SLDPRT, 36-24342-ND.SLDPRT, 605zz.SLDPRT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]
2021-12-20 Fix nodes (#2)
    * Fix the low pass filter for face_following and sound_following.
    * Fix node names
    * Fix explore_node and gesture_node.
    * Fix command frequency
    * Fix rtabmap launch
    * Fix sound_following
    * Fix face_following
    * Fix talk
    * Fix person_identification.
2021-12-20 Add battery cable assembly steps. Fix the battery holder. (#3)
    [base audio.SLDASM, base disk.SLDASM, base mic.SLDASM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]
2022-01-10 Hbba lite (#4)
    * Refactor c++ filters.
    * Add desire classes.
    * Add motivation base classes
    * Add Stategy
    * Add RosStrategy
    * Refactoring, add HbbaLite class.
    * Add gecode for CSP. Set the target of the sound_following and the face_following even if all messages are filtered.
    * Add GecodeSolver
    * Fix DesireSet
    * Add filter contraints.
    * Add FilterConfiguration static method onOff and throttling.
    * Refactoring
    [main.cpp]
2022-01-20 Demos (#6)
    * Add the UI of the control panel
    * Add desire creation
    * Add strategies.
    * Update the README
    * Refactor T-Top desires and stategies.
    * Add smart_speaker demo.
    * Add French support in smart_speaker. Add readme and launch files.
    * Add comments
    * Add EER to RocEvaluation
    * Fix launch files
    * Fix BehaviorsTab
    * Fix launch files.
    * Remove useless header includes
    [main.cpp]
2022-01-27 Fix smart speaker (#7)
    * Fix smark speaker
    * Improve simple face animation.
    * Reduce the text for the current weather
    * Wait the song start before dancing.
    * Make the face_following and sound following faster. Reduce the number of repetition for yes, no and maybe.
    * Fix person_identification_node.py
    * Update audio_utils. Change SSS frame sample count to 2048.
    * Fix robot_name_detector_node.py to always calculate the sound_rms value.
    * Add a reload when the rosbridge closes.
    * Add min_activity to sound_following
    * Fix dnn_utils test.py
    * Add test_multiclass_audio_descriptor_extractor
    * Reduce sound_rms_release
    [configuration_16SoundsUSB.cfg]
2022-01-27 Update Standoff (#9)
2022-02-07 Fix base disk (#10)
    * reduce the diameter of the base disk
    * Update robot.STEP
    [base disk.DXF, base disk.SLDASM, base disk.SLDPRT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]
2022-02-25 Assembly (#16)
    * Fix speaker cables
    * Add Audio Base Pre-Assembly steps
    * Fix seaker images.
    * Fix typo
    * Fix psu_control firmware
    * Fix MCU communication.
    * Add base disk, audio base assembly steps.
    * Finish the assembly steps
    * Update 11_ROBOT_ASSEMBLY.md
    * Fix PCB issues
    * Add the hbba_lite doc
    [buck_boost-B_Cu.gbl, buck_boost-B_Mask.gbs, buck_boost-B_Paste.gbp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]
2022-03-08 Stewart forward kinematics - Replace the neural network by the Trust Region Reflective Algorithm (#19)
    * Switch to analytic forward kinematics.
    * Cleanup
    * Cleanup
    * Add SERVO_ANGLE_MIN and SERVO_ANGLE_MAX to the opencr code.
    * Update README.md
    * Fix bugs
    * Use analytical Jacobian calculation.
    * Fix opencr parameter generation
    * Update the opencr firmware to remove the NN (refs #12).
    * Fix the opencr code generation
    * Reduce the head tolerance
    * Fix solver
    * Fix solver
    * Update readme.md
    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
    [StewartForwardKinematics.cpp, StewartInverseKinematics.cpp, StewartKinematicsParameters.cpp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]
2022-03-16 Added opentera behavior
    [configuration_16SoundsUSB_pa.cfg, configuration_16SoundsUSB_pa_echo_cancelled.cfg]
2022-03-16 Fixed code review elements
    [configuration_16SoundsUSB_pulseaudio.cfg, configuration_16SoundsUSB_pulseaudio_ec.cfg]
2022-03-22 Format (#23)
    * Format
    * Update audio_utils
    * Update .clang-format
    * Revert package-lock.json
    [Buzzer.cpp, Fan.cpp]
2022-03-23 Refactoring (#24)
    * Fix BatteryLed
    * Add missing remap fot dance_node.py
    * Update BOM
    * Rename *frame to *frame_id
    * Rename *frame to *frameId
    * Move the HBBA Desires and Strategies to another ROS package #14
    [main.cpp]
2022-04-20 Support for opentera online (#27)
    * Support for opentera online
    * Reduced Realsense frequency to 15 Hz
    * Added real robot_status
    * Fix firmware
    * Fix robot_status
    * Replace isBatteryCharging by isPsuConnected.
    * Add isBatteryCharging
    * Fix ControlPanel
    * Add the step for the teensy udev rule
    * Fix base_status in robot_status
    * Add localisation arg to the rtabmap launch file
    * WIP rtabmap and rviz
    * WIP rtabmap
    * Fix odas dynamic linking error
    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
    [ttop.urdf.xacro]
2022-04-27 Improve face following speech to text gesture (#30)
    * Change face height target in face_following, use interim_results in speech_to_text
    * reset TARGET_HEAD_IMAGE_Y
    * Use screen output for HHBA nodes
    * Add a timeout for the gestures.
    * Add a timeout for the gestures.
    * Add a cache to the talk node
    * Remove wrong import
    * Switch to InvalidTaskState if a transcript has been received.
    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
2022-05-04 Fix BOM tables (#32)
2022-05-06 Add the SSD in the BOM (#33)
2022-05-19 Ego noise (#35)
    * Add the ego noise opencr firmware
    * Update the opencr firmware
    * Fix movement_commands.py
    * Add libgfortran-*-dev as dependancies
    * Add ego_noise_reduction/data_gathering.py
    * Add missing things in ego_noise_reduction
    * Fix data_gathering.py
    * Fix data_gathering.py
    * Fix data_gathering.py
    * Fix data_gathering.py
    * Fix data_gathering.py
    * Update ego_noise_opencr_firmware.ino and data_gathering.py.
    * Fix the data gathering.
    * Fix the data gathering.
    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
    [configuration_16SoundsUSB.cfg, configuration_16SoundsUSB_pulseaudio.cfg, configuration_16SoundsUSB_pulseaudio_ec.cfg]
2022-05-20 Improve sound following (#37)
    * Improve sound_following_node.py
    * Add missing filter state check in face_following_node.py
    * Reduce the frequency of static transform publishers.
2022-05-23 Add specific person following (#38)
    * Add status
    * Add the missing doc. Remove the TODOs.
    * Reformat the code
    * Fix SpecificFaceFollowingStrategy
    * Disable browser with control_panel
    * Fix Strategies.cpp
    * Fix Strategies.cpp
    * Fix specific_face_following_node.py
    * Fix specific_face_following_node.py
    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
    [main.cpp]
2022-06-06 Refactor video_analyzer to support RGB and RGB-D camera. (#39)
    * Refactor video_analyzer to support RGB and RGB-D camera.
    * Fix README.md
2022-07-01 Wide angle camera (#44)
    * Add the wide angle camera in the CAD and the BOM.
    * Change launch files for the second camera. Add the desires and strategies for the second camera.
    * Add object sizes in the video analysis
    * Add sound_object_person_following ros nodes. Update control_panel. The sound_object_person_following_node is not finished.
    * Add the missing code in ObjectPersonFollower._find_target.
    * Fix 2d wide camera calibration
    * Fix control_panel
    * Fix control_panel
    * Fix sound_object_person_following.launch
    * Fix sound_object_person_following_node.py
    * Fix camera_2d_wide capture. Fix sound_object_person_following_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
    [Intel RealSense D435i.SLDPRT, M2.5x5mm plastic.SLDPRT, head cable protector.SLDPRT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]
2022-07-17 Add audio frame header (#46)
    * first version for backup
    * moved at the right place
    * installing python script
    * Added setup.py
    * working transcoder
    * Fix review comments
    * Add audio frame header supports.
    * Use 16 kHz audio every where.
    * Fix issues
    * Fix music beat detector
    * Add missing output=screen
    * Fix smart_speaker replay and transcode launch files
    * Added video frame latency due to RealSense D435 wrong timestamp
    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
    [configuration_16SoundsUSB.cfg]
2022-08-24 Fix audio clip (#48)
    * Fix buffer overflows and frame splits.
    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
2022-09-12 Jetson setup (#49)
    * Add assembly steps to configure the computer. Fix DNN.
    * Fix computer configuration
    * Fix realsense
2022-09-15 Home logger (#50)
    * Add home_logger and recorders packages.
    * Fix software encoder in video_recorder_node.py
    * Fix software encoder in video_recorder_node.py
    * Fix multichannel audio in video_recorder_node.py
    * Fix multichannel audio in video_recorder_node.py
    * Cahnge h265 to vp9.
    * Add perception_logger_node
    * Format the code
    * Fix smart_speaker_smart.launch
    * Fix State::State
    * Fix perception_logger_node
    * Fix perception_logger_node
    * Fix perception_logger_node
    * Use bindNoCopy instead of bind for blob and string.
    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
    [main.cpp]
2022-10-27 Fix the framerate of the wide angle camera
2023-07-17 t top v4 (#76)
    * Add the CAD files of the base.
    * Add Jetson AGX Orin
    * Move torso magnets to the outer diameter.
    * Rename support to bracket
    * Add stewart bottom
    * Fix torso bottom holder
    * Add the head onto the stewart platform. Add the stewart platform onto the robots.
    * Add magnets on the head
    * Add stewart springs.
    * Apply comments
    * Fix CAD. Add STL.
    * Rename CAD_v4 to CAD
    * Update buck_boost to kicad 6
    * Add first draft of psu_control
    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
    [Jetson AGX Orin.SLDPRT, LED level diffuser.SLDPRT, LED level.SLDPRT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]
2023-09-22 Connect4 (#81)
    * Add the connect4 demo.
    * Update the demo README.md file.
    * Add the installation of C++ torchvision.
    * Add incoming face cropping.
    * Add video recording in the connect4 demo.
    * Update jetson_configuration.sh
    * Update jetson_configuration.sh
    * Update opentera-webrtc-ros
    * Update jetson_configuration.sh
    * Update jetson_configuration.sh
    * Fix video recorder codecs.
    * Update 01_COMPUTER_CONFIGURATION.md
    * Fix Connect4 crash
    * Update opentera webrtc ros
    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
2023-09-29 Add Piper TTS and, Whisper ASR (#80)
    * Modified the process of CachedVoiceGenerator
    * Add the piper_ros package.
    * Added voice type
    * Added gender to launch file
    * Add ONNX Runtime install steps.
    * Update the demos strings to make them compatible with piper_ros.
    * Remove non-talk related changes.
    * Update the talk node to use piper. Update launch files.
    * Add a parameter to use the GPU or not.
    * Add the models license.
    * Add the VAD. Add whisper_speecg_to_text.py.
    * Fix control_panel and launch files.
    * Update audio_utils.
    * Fix the Jetson Orin name in the main readme. Fix the device name for the cpu. Fix high CPU usage after the transcripti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
2023-10-25 Fix mechanical parts (#82)
    * Fix battery holder and torso bottom internal parts.
    * Fix assembly steps.
    * Update 06_AUDIO_BASE_ASSEMBLY.md
    [base disk.SLDASM, battery holder.SLDPRT, battery holder.STL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]
2023-11-15 Improve dnn (#74)
    * Update pose_estimor and face_descriptor_extractor
    * Fix heatmap_sigma type
    * Improve face alignment, fix face_descriptor extractor training.
    * Improve audio analyzer (ref #70).
    * Improve video analyzer (ref #68)
    * Update HBBA lite.
    * Update video analysis and audio analysis loggers.
    * Add HBBA strategies log to the perception logger.
    * Rename blur score to sharpness score.
    * Add distillation_loss_alpha to train_pose_estimator.py
    * Add distillation_loss_alpha to output path.
    * Fix trainers for criterion next_epoch. Fix export_yolo_v4. Add GPU support to align_faces.py and test_pose_estimator_with_yolo_v4.py.
    * Fix OpenFaceBackbone
    * A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
    [configuration_16SoundsUSB.cfg]
2023-12-10 Ubc demo (#83)
    * Disable semantic segmentation.
    * Add pose classification.
    * Remove prints.
    * Increased timeout to 20 sec and use google cloud url. Use wide angle camera for pose classification.
    * Decrease presence threshold
    * Cache size is now 1000
    * Add missing readme for pose_classifier.
    * Add the first draft of the behavior led_animations
    * Fix build with catkin build.
    * Fix Led tab buttons.
    * Add arguments for video_analyzer in bringup.launch
    * Update tab_leds.png in control_panel.
    * Improve robot name detection.
    * Add LED status in robot_name_detector.
    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
    [config.h]
2024-02-06 Connect4 v2 (#87)
    * Fix createRobotNameDetectorWithLedStatusDesireStrategy
    * Add prebuffering to whisper_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
2024-04-03 fix whisper residual samples that give garbage (#89)
    * fix whisper residual samples that give garbage
    * Removed ROS print
    ---------
2024-04-15 Speech stats (#92)
    * Added stats to transcript
    * Fixing google processing time and sample count
    * Updated time, looks more than the response time than the processing time since the last final sentence
    * Adding processing time to analysis message
    * Adding processing time to video analysis.
    * Adding stats to talk node
    * Fix frame publisher
    * Moved stats into a function
    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
2024-05-09 Fix teensy compiler version (#100)
    * Build the user interface at build time.
    * Reduce the sleep duration
    * Adding delays when launching nodes.
    * add more delays
    * Working on ARM
    * Fix version for ARM
    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
2024-11-08 Ros2 migration (#106)
    * Remove all ros1 nodes.
    * Add ros2 submodules.
    * Ignore system projects.
    * Add cloud_data.
    * Add dnn_utils
    * Add daemon_ros_client
    * Add audio_analyzer.
    * Add video_analyzer
    * Add pose_classifier.
    * Add robot_name_detector.
    * Add speech_to_text
    * Update submodule
    * Update daemon_ros_client_node.cpp
    * Add t_top without launch. Refatoring.
    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
    [configuration_16SoundsUSB.cfg, ttop.urdf.xacro]
2025-02-20 Fix warnings (#108)
    * Fix warnings
    * Fix warnings in submodules
    * Hide npm warnings if the user_interface build is a success
    * Fix duplicate tf, npm no longer clear terminal
    * Fix install script for t-top v4 for ROS2, jetson orin and jetpack 5.1.4
    * Update submodules
2025-05-13 Integration of chat llm behavior (#112)
    * skeleton
    * Adding ChatDesire and ChatStrategy, WIP.
    * Base chatbot demo
    * Demo enabling ChatStrategy working. WIP.
    * Working chat with ollama
    * Working chatbot
    * Updated to ros2 branch
    * Working ChatGPT with function calls, WIP.
    * Working simple function calls
    * Starting separation into configuration files
    * Sending function calls from tools to publisher
    * Calling external services, WIP
    * Calling external services, WIP
    * WIP, adding service to chatbot demo
    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
2025-07-14 Added Chatbot capabilities (#116)
    * Callbacks blocking after calling service, why ?
    * Trying another thread, same result, not receiving subscriber message
    * Workaround to avoid service call blocking the executor
    * Workin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
2025-09-05 Update Chatbot (#121)
    * Working version to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
